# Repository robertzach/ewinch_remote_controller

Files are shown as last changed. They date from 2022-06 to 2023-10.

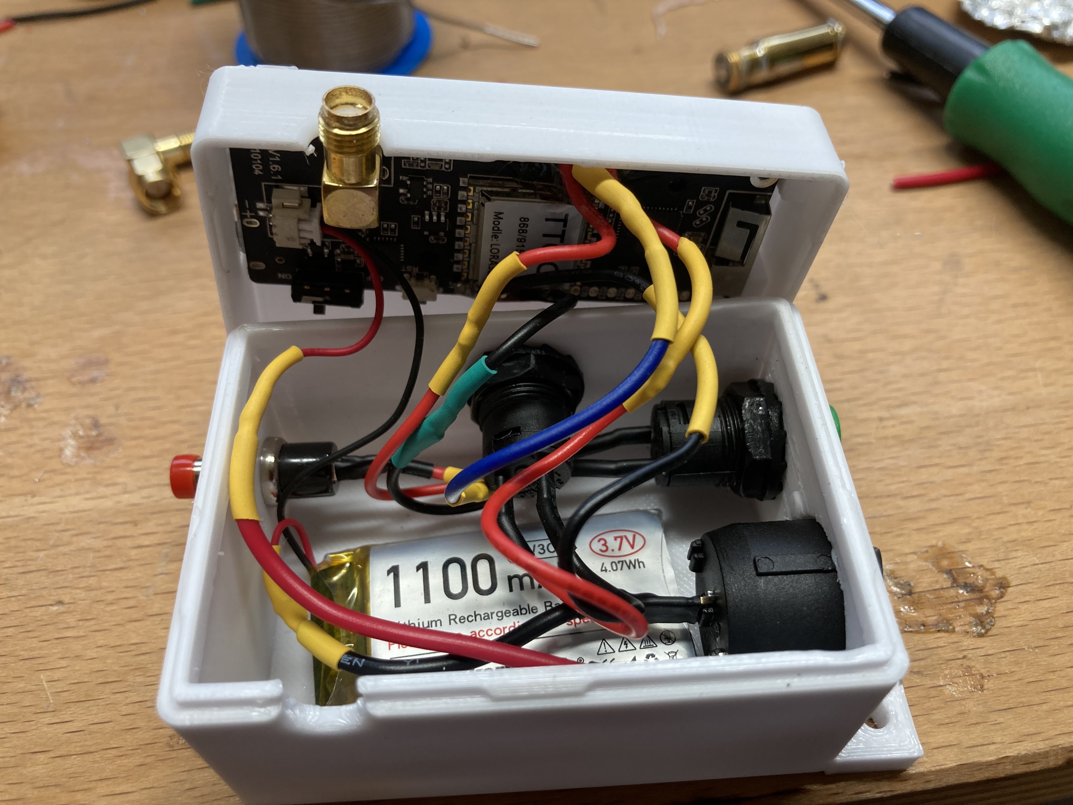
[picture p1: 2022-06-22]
doc/transmitter_cabels.jpg

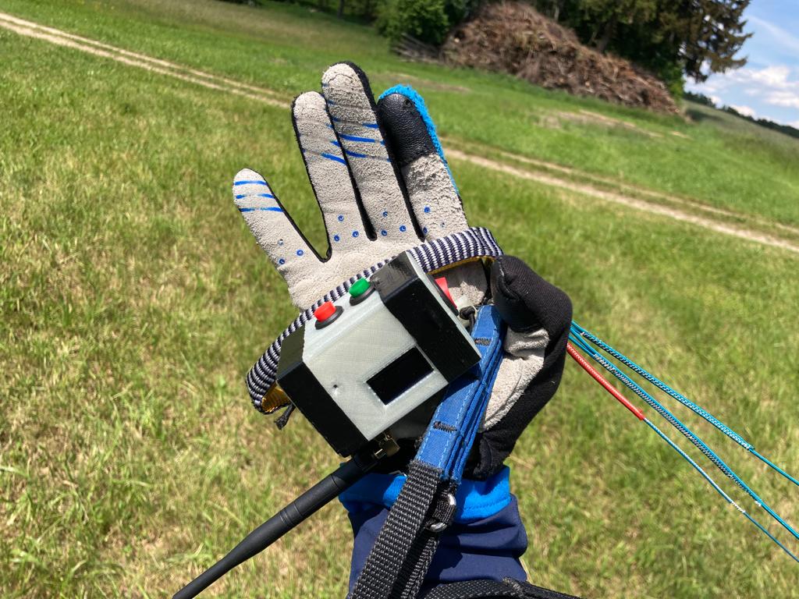
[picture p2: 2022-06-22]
doc/transmitter.jpg

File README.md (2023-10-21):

# ewinch_remote_controller
 transmitter and receiver code for remote controlling a paragliding winch
 Based on LILYGO® TTGO ESP32-Paxcounter LoRa32 V2.1 1.6 Version 915MHZ LoRa ESP-32 OLED
 (http://www.lilygo.cn/prod_view.aspx?TypeId=50060&Id=1271&FId=t3:50060:3)
 
 see 
 - https://www.youtube.com/watch?v=hUOhuwIBEUY
 - https://www.youtube.com/watch?v=hVimrIMGMSY&t=1s
 - https://www.youtube.com/watch?v=DOm1zkXft44
 - https://www.youtube.com/watch?v=bxIVrh16ZTE
 - https://www.youtube.com/watch?v=qTut_0KAwYU

 receiver uses PPM for driving the winch and (optinal) UART to read additional information (line length, battery %, dutycycle)
 VESC UART communication depends on https://github.com/SolidGeek/VescUart/

Pin Setup receiver:
PWM_PIN_OUT  13
VESC_RX  14    //connect to TX on Vesc
VESC_TX  2    //connect to RX on Vesc

transmitter buttons connected to GND:
BUTTON_UP  15 
BUTTON_DOWN  12

Line auto stop can be implemented within VESC with vesc_ppm_auto_stop.patch
Default VESC app config is vesc_app_config.xml

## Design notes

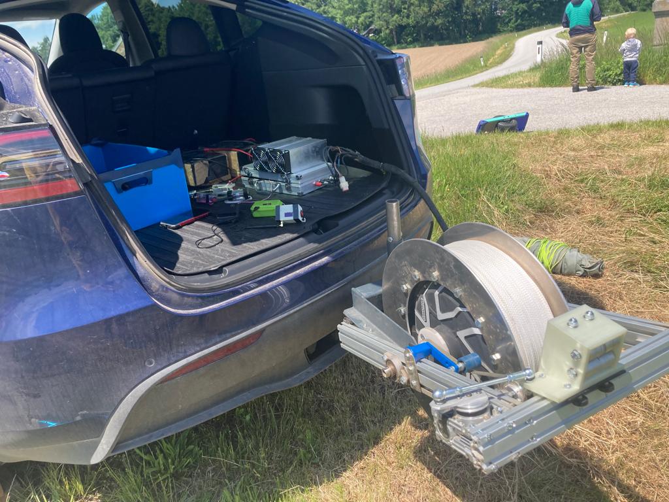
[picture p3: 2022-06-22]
doc/winch.jpg

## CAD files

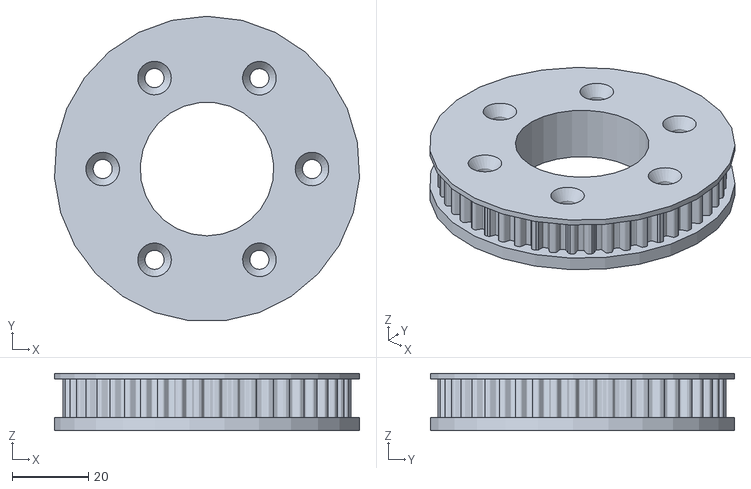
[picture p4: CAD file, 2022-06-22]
stl/belt_drive_B.stl
79.9 x 79.7 x 15.0

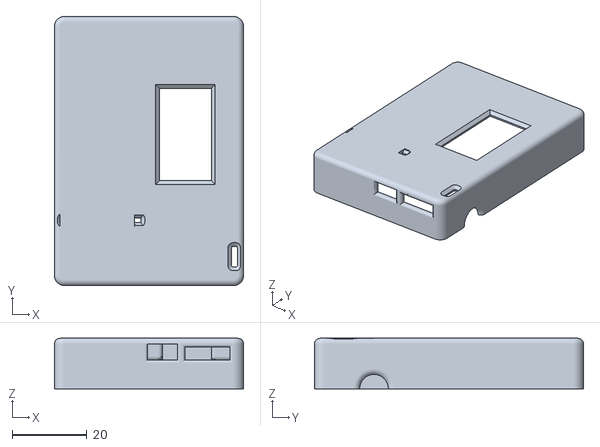
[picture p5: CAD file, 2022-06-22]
stl/transmitter_top.stl
50.6 x 71.9 x 13.5

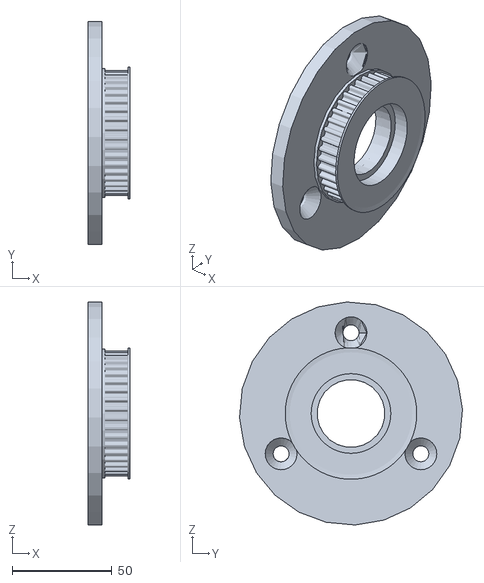
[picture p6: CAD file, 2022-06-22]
stl/belt_drive_A.stl
21.3 x 111.9 x 111.9

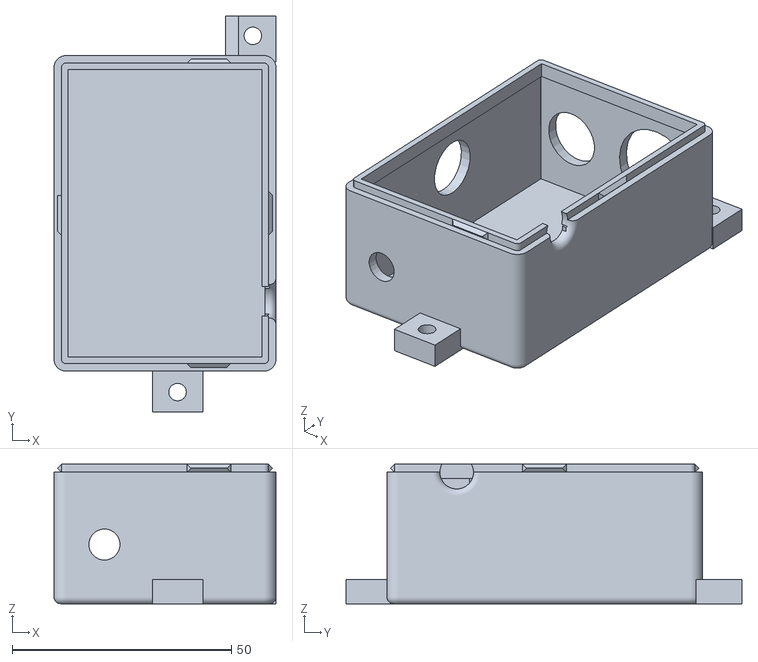
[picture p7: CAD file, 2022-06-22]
stl/transmitter_bottom.stl
50.6 x 90.2 x 31.8

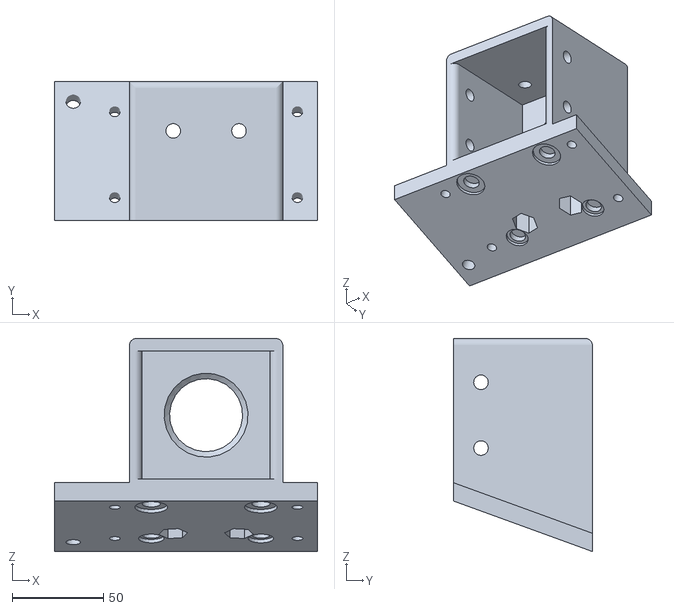
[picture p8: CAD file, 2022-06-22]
stl/cable_guide.stl
144.0 x 76.0 x 116.7

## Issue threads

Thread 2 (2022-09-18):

Battery Config / Voltage

looxis-renaud, 2022-09-18:
Not really an issue on the remote controller itself - but without the winch, there's no need for the remote :-)
why re-invent the wheel, so my plan is to build the winch exactly as you did, with the same components.

In one of your youtube comments you state that you use 2x 8S10P battery packs made from INR21700 cells.
Are you connecting the two packs in parallel (28,8 Volt) or in series (57,6 Volt) ?

looxis-renaud, 2022-09-18:
found the answer in the youtube comments :-)

> [@siffer siffer ](https://www.youtube.com/channel/UCgYK9i93dRLXB5Vw_T8CE_Q) see the pics in the link. twice 8s10p in series without BMS. 8s can be charged with common RC chargers...
>
> https://drive.google.com/drive/folders/1BV3k2qoKL2DN3fKvVQ9Kf_huecXmPUIT

Closed 2022-09-18.

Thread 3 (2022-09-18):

Motor

looxis-renaud, 2022-09-18:
In one of the youtube comments you mentioned that you are using the QS Motor 12kw,
available here: https://www.aliexpress.com/item/4001237537247.html

Do you use the **"72V"** or the **"96V"** version ?

robertzach, 2022-10-17:
Chinese supplier are a bit confusing with their order options.
The main thing is the "KV" value which describes the rpm / voltage relation.
rpm = KV * voltage

Therefore, it depends on what battery voltage you use.
With a 16s lion battery (what I use) you have around 16*3,7 --> 60V.
For this case I recommend the 72V option (72V @ 1047RPM --> KV = 14).

steve1428, 2023-04-05:
be careful, I Found some other people representing themselves as QS motor when they weren't.  Deal with them directly.

Closed 2022-10-17.

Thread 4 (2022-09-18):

automatic brake with 15m of cable left

looxis-renaud, 2022-09-18:
How does the controller know after release, that it is time to brake because the line has only 15m left?

Is that calculated based on number of rotations of the drum, or is there a (magnetic) sensor on the cable, that detects the last 15m ?

robertzach, 2022-10-17:
the controller counts the rotations... it is very accurate!

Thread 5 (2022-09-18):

Which firmware for VESC Controller?

looxis-renaud, 2022-09-18:
VESC is controlling the brushless DC motor - do you use the standard VESC Firmware
or a fork? Asking this question because in one of your youtube videos you mention "Skypuff" which seems to be a fork of VESC standard firmware. I found this: https://github.com/talkyoo/vesc_tool_skypuff

robertzach, 2022-10-17:
It uses standard Vesc. e.g. 5.3.
Autostop is only supported with some changes in the standard vesc code:
see vesc/vesc_ppm_auto_stop.patch

looxis-renaud, 2022-10-18:
Hello Robert, I assume I could just use /vesc/vesc_75_300_auto_stop.bin,
which is probably the newly compiled VESC firmware including your vesc/vesc_ppm_auto_stop.patch ?

I do have the VESC 75/300.

_______
yes, I do not have any coding skills, I am just able to read and possibly understand the most basic code...

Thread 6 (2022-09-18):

parts needed for controlling the brushless DC Motor?

looxis-renaud, 2022-09-18:
watching your videos, I assume one needs the following electronics to control a brushless dc motor:

* VESC Controller
* Receiver: 1x LILYGO® TTGO ESP32-Paxcounter connected with VESC
* Transceiver 2x LILYGO® TTGO ESP32-Paxcounter, 1x Master & 1x Slave

Is this correct, or is anything else needed?

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

robertzach, 2022-10-17:
basically yes.
If multiple transmitter are used I would describe it as "admin" and "user" transmitters...

Closed 2022-10-17.

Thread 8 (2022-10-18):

Cable Guide parts

looxis-renaud, 2022-10-18:
I'd be happy to get some help on your cable guide.

I started a parts list for others to possibly follow up, but some of the parts are still unclear: https://github.com/looxis-renaud/ewinch_remote_controller/blob/main/doc/parts-list.md

It looks like you're using a worm gear. Any words on the gear ratio and the other parts that you used?

looxis-renaud, 2023-02-22:
I am not quite there yet, but in the meantime I am favoring a "level winder / barrel cam mechanism" as seen here: https://www.youtube.com/shorts/LLIwVdaRViM

Closed 2023-03-02.

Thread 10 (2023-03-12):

Moving "AutoStop" function from VESC to Receiver

looxis-renaud, 2023-03-12:
Since the receiver has Tachometer Data through the UART connection and "knows" the line length,
why not move the "AutoSTOP" feature from the VESC to the Receiver?

The Receiver is already controlling the winch, why not also let it execute the AutoStop when the line has only ~15m left?

The advantage would be that we could use the latest VESC firmware, without having to constantly change it by adding the Autostop feature ( I can't get the modified firmware to run anyways, see #9 )

robertzach, 2023-03-12:
It is already implemented it in the receiver code too (see line 277 to 292).
But it is slow (UART) and not 100% reliable (and you want 100%!).

See https://github.com/robertzach/ewinch_remote_controller/blob/main/receiver/receiver.ino:
      // auto line stop
      // (smouth to avoid line issues on main winch with rewinding winch)
      // tachometer > 2 --> avoid autostop when no tachometer values are read from uart (--> 0)
      if (vescUART.data.tachometer > 2 && vescUART.data.tachometer < 40) {
          if (targetPullValue > defaultPull){
              targetPullValue = defaultPull;
          }
          if (vescUART.data.tachometer < 20) {
              targetPullValue = softBrake;
          }
          if (vescUART.data.tachometer < 10) {
              targetPullValue = hardBrake;
          }
          Serial.println("Autostop active, target pull value:");
          Serial.println(targetPullValue);
      }

Closed 2023-03-12.

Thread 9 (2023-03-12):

vesc_75_300_auto_stop.bin makes the motor spin without stopping

looxis-renaud, 2023-03-12:
Hello Robert,
I had no luck flashing this firmware onto the VESC 75/300.
once you start setting up the input with this firmware, the motor just starts spinning and isn't controllable with your remote.
It does work with the original firmware, though (just no autostop then...)

I assume this is because of this function:

```
        // my default pull
        // manualy regulate pull with a poti on ADC2
        // in manual pull mode autostop only on demand (to rewind the last meters cable...)
   #ifdef ADC_IND_EXT2
     if ( (((float)ADC_Value[ADC_IND_EXT2])/4095) * V_REG > 0.5) {
     my_default_pull = ((((float)ADC_Value[ADC_IND_EXT2])/4095) * V_REG - 0.5) * 30;	//0 - 100% after 0.5V
        // set default pull value
     mc_interface_set_current(my_default_pull * 0.35);	//0 - 35A
```

This sounds like as it would be an early version of your code, where you were using a potentiometer to test the motor?
ADC2 input is not used, it's the PPM input that's being used... which has no ability to control the motor with this firmware.

I am just speculating here... sorry to bother.

robertzach, 2023-03-12:
I have a poti on ADC2 to manually control the winch. E.g. To wind up the last meters of the line when finishing. Or to set a tension when used as a rewind winch...

If you do not install one, just connect ADC2 to GND.

looxis-renaud, 2023-03-27:
@robertzach , can you tell me what specifications your potentiometer has ? i.e. the resistance, like 0,1, 1, 10 or even 100 kOhm ?

Closed 2023-03-12.

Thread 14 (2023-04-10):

ESP32 version?

steve1428, 2023-04-10:
code is sticking on esp32 version

cannot find crt1-sim.o: No such file or directory

do we know what version this code used?

steve1428, 2023-04-11:
just had to add esp-32 in preferences board manager urls

Closed 2023-04-11.

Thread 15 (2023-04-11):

work for hall

steve1428, 2023-04-11:
do you think the code will work for a hall sensor motor?
it looks like it was written for AS5047 SPI encoder

Closed 2023-04-14.

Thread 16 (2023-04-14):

No display, nothing happening

steve1428, 2023-04-14:
We got the ttgo t3 v 1.6.1 esp32 lora.  We found all the libraries and got the code to compile.  Tried loading the binary files as well as the code directly from arduino

no display working.
Try the Tx up down buttons, no pwm signals on the Rx pinout
there is an issue with ssd1306 library maybe and commands to setup the display?
the adafruit example sketch for 128X32 I2C works no problem, we can blink led etc so controller is working.
was there also supposed to include adafruit_1360 and gfx libraries maybe?

steve1428, 2023-04-15:
OLED pins are 21 and 22 on the controller, change in lines 84 thru 88 in the transmitter code and appropriate in receiver code.
we have display now but it's blinking on and off all the time

Closed 2023-04-15.

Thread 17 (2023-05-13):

VESC: Motor is "pumping" under heavy load, is this normal?

looxis-renaud, 2023-05-13:
Sorry Robert to bother you again.
I am ready to make a test flight, but we're having an issue:
 we wanted to test the motor's drag force according to the defined force in the remote, before we are actually going to launch ourselves.

We attached a "Quad" (a motorcycle with 4 wheels) to the line and started pulling. To measure the drag force in kilogram (or daN) we were using heavily the brake of the quad.

As you can see in this video: https://youtu.be/rusCd4p7q5k
the Motor is pumping /oscillating heavily under load.

When driving backwards under load, the winch was nicely unwinding the line, no issues with oscillation.

Is this possibly because of the inertia of the quad and because of the resistance of the wheels on the bumby grass?

Have you not experienced something similar?
Could this possibly be solved with some settings in the VESC app?

Thank you in advance for any help.

robertzach, 2023-05-15:
Looks like your VESC motor configuration is not very stable.
You can compare the pid values with the following config: https://github.com/robertzach/ewinch_remote_controller/blob/main/vesc/vesc_motor_config_12kw_260_V4.xml
Furthermore it is import that your winch is mounted on a more solid point to avoid oscillation!!
You can call me at +43 664 2314337, I may can give you some hints on the VESC motor config.
PS: Please also let me know were you got your thread for the line guide from? It looks really nice!

looxis-renaud, 2023-05-16:
Hi Robert,
thanks again, as always, for your valuable feedback. will check the VESC settings again and also give you a call.

The "line guide" or "winding mechanism" was purchased from https://www.ebinger-gmbh.com/
It's the model 1.610.010 >>automatische Schlauchführung, Stahl lackiert, 1/2" -/ 5/8" Schlauch für Modell OSM 610<<.
It's intended purpose is for water hoses or compressed air hoses and was modified by a friend of mine to accommodate for the thin dyneema line and the width of the drum.

Closed 2023-05-16.

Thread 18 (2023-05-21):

pinmode set for button up / dn

steve1428, 2023-05-21:
hi can you tell me please if pin 15 / 12 are internal pullup?
I can't see in the code.

is it possible to change to internal pulldown so we can trigger it with an external 3.3V signal?

robertzach, 2023-05-23:
yes, both use a internal pull up. I am not sure if you can reprogram it. Google is your friend :-).
Fast solutions would be a external 1k resistor to GND or use a different pin...

Closed 2023-05-23.

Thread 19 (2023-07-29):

Skalierung der Leistung

Logo66, 2023-07-29:
Hallo Robert Microkontroler programmieren usw. ist Neuland für mich. Habe eigentlich fast alles hingekriegt aber das eine oder andere versteh ich noch nicht ganz. z.B
In der Anweisung für PPM-Einstellungen heißt es: „static int myMaxPull = 85; // 0 – 127 [kg], muss mit den VESC-ppm-Einstellungen skaliert werden.“ Wie wird dies eingestellt oder kalibriert?

https://photos.app.goo.gl/PnyRyFPGkBvydZn87

steve1428, 2023-07-29:
I think he means you just vary the pull amount in the code depending on
your particular motor's power
if you notice he's made two of them so he can use the other one in braking
mode to test and set things up, otherwise you have to go out in a field and
do test pulls.
I've got mine all working I just need to 3D print the hand held controller
case because I can't find anything appropriate off the shelf
https://youtu.be/9rqX89-msBY

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

Logo66, 2023-07-29:
https://a360.co/3Dy5PxJ

Ich habe mir diesen gedruckt.

steve1428, 2023-07-29:
Das ist wunderschön !

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

steve1428, 2023-07-29:
https://d-splicer.com/d-splicer-set-kit/

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

robertzach, 2023-07-29:
Depending on your motor (power, KV value, diameter, etc.) you need to scale the resulting kg pull on your line.
I think the best way is to adapt the "Motor Current Max" and "Motor Current Max Brake" value in the Vesc Motor Settings (General -> Current).
You could also adapt the "Pulselength Start" and "Pulselength End" in the Vesc App settings (PPM -> Mapping) to reach the same goal.
I used a suitcase scale to measure the real pull on the line.
With my QS260 hub motor I have around ~3,6A/kg pull.

Logo66, 2023-07-29:
Danke Robert das hat mir weiter geholfen.

Closed 2023-07-29.

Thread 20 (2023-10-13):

QS motor

lamaatje, 2023-10-13:
Hi Robert,

In understand you use a 12kW QS motor 13" by 4.5" is that correct?
Did you order a specific variant optimized for torque?

Kind regards,
Stefan

robertzach, 2023-10-16:
I used https://de.aliexpress.com/item/4001237537247.html?gatewayAdapt=glo2deu
with standard config.
I reach about 60 km/h with my 16s battery and a pull force about 70kg with about 240A.

steve1428, 2023-10-16:
I shorted my trampa vesc trying to setup on my electric unicycle, we tried
solder new mosfets but didn't work.
There is cheaper vesc from India now

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

lamaatje, 2023-10-16:
Hi Robert,

Thanks for the response. I am looking for an appropriate motor it is my
understanding that many of those hub motors used in scooter/motorbike
applications are optimized for speed.
So am looking for something with high Kt [Nm/A] and high rated current.
I have a second hand QS motor that just does that but it does not have a
type tag. I can pull 70kg with 100A with a radius of .25m
this means 700/4= 125Nm @ 100A -> Kt = 1,25 Nm/A.
I am not sure what you diameter is but lets also take .25m than your
motors Kt = 125/240 = 0,52 Nm/A.  Since motor dissipation is mainly due
to copper loss I2R, lower current is very desirable to avoid motor
heating. Of course with low R heating can also be avoided that is why it
is important to know the rated current. For your motor I understand that
this is 167A so that means it will heat up considerable.
Can you confirm this?

Kind regards,

Stefan

robertzach schreef op 2023-10-16 10:10:
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

steve1428, 2023-10-16:
yup, hub motors aren't really designed for high torque applications so they
get hot.
setup a fan and keep an eye on the temps.
If you look at other winch projects on youtube some guys are using other
motor types.

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

lamaatje, 2023-10-16:
Well there is not a fundamental reason why they could not be optimized for torque and since they have high pole pairs counts they can deliver quite a lot of power in the RPM range for a paraglider winch applications. Although the high rotational inertia is also a big disadvantage. The big advantage is direct drive. Do you have some pointers wrt other QS motor or hub motors in general?

steve1428, 2023-10-16:
yes they do make very high torque BLDC motors..... the leperkim veteran
patton electric unicycle (126V) I just bought has enough torque to spin the
wheel when you climb a hill, it's a beast.

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

robertzach, 2023-10-16:
**If you want to do step tows you need some speed to be safe when flying back!!!**
If you do no step tows you can go down with the speed to around 40km/h -> choose a hub motor with lower KV value (more torque optimized)
My first winch was calculated for max speed around 40 km/h (see https://www.youtube.com/watch?v=E3TgccQ8CuA).
It also depends on what battery you want to use.
Right now I am using 16s which is 66V on full charge. This keep my battery setup easy.
For my first winch I increased to 22s (90V) to get more speed.
To sum up, battery/controller/motor needs to be chosen in the right mix, depending on your speed (step tows?) and pull (weight?) requirements.

lamaatje, 2023-10-16:
Hi Robert,
I have to disagree. When step towing and flying away from the winch the motor just needs to brake. The torque is opposite to the rotation direction so you will be generating power. E.g. say you fly away from the winch with 15 m/s and the tow force is 40N (towards the winch ie the same direction as when doing a tow) you will be generating 600W. Assuming no losses for simplicity, if your battery is 60V you will be charging it with 10A.

Towing requirements are simple in zero wind conditions 10 m/s @ 1000N. So 10kW mechanical power.  So a 12 kW rated motor should be able to do the job. 12kW is the electrical rating assuming 10/12=83% efficiency at the rated mechanical power this is realistic. Depending on your spool radius you need a motor with the proper Torque, speed curve where the RPM at maximum power is at 10 m/s. For a radius of 0.2m that would be 477 RPM and 200Nm.

steve1428, 2023-10-16:
12KW is plenty of power regardless

I've got the QS motor 3/5 kw motor and I know people are able to get it to
work

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

robertzach, 2023-10-17:
I recommend you https://en.wikipedia.org/wiki/Motor_constants
Max speed is defined by KV = speed / Voltage.
The only way to increase speed above the limit based on KV and Voltage is to use field weakening.
But field weakening is still beta in VESC and in my tests it only increased the max. speed with my hub motors around 20%.
I would not recommend to used field weakening to increase max. speed for flying away on step tows.
If anything fails you can get in big trouble....

lamaatje, 2023-10-17:
I think you are missing the point here. All these things like field weakening to increase speed are applicable when the motor is **driving**. When you fly away from the winch the motor is not supposed to be driving it is supposed to be **breaking**.  If you look to it from another perspective: suppose that you completely shut down the motor control when you fly away from the winch will your speed be limited? I think the answer is no. Is it is also not desirable because you need some force to limit slack of the line and make sure the line stays on the spool. You can do this by letting the motor brake a bit this can be done at rpm's way higher than the rpm's in the range were the motor is driven. You have to basically control the current the motor is **generating** (NB not consuming) and the best way is to have the current back in the battery (regen braking). The speed range were you can do regen braking is much higher and mainly voltage limited. I have this working on my controller and it works just fine.

lamaatje, 2023-10-17:
> 12KW is plenty of power regardless I've got the QS motor 3/5 kw motor and I know people are able to get it to work
> […](#)
Sure, with a little bit of head wind, low pilot weight, low ascend rate. But that is not the point. If your motor is capable of a certain sustainable mechanical power you want to dimension it in such a way that it gives that output in a range that is optimal for towing that's why you do the math.

robertzach, 2023-10-17:
> when you fly away from the winch will your speed be limited? I think the answer is no

This is wrong. For brushless motor rpm and voltage are in direct correlation.
Therefore, when you increase the motor rpm (when flying away) above the limit (which is the voltage of the controller) the controller will burn. By using field weakening you can push this limit a bit, but any issue will immediately burn the controller.
When you burn the controller when flying away I wish you that the lines on the spool do not get messed up.
Yes, it is possible to a 5kW hub motor, but you will be very likely limited with speed supported...

steve1428, 2023-10-17:
doesn't the BMS deal with the regen current?  This is a problem with
electric unicycles going down hill after a full charge.
as long as the battery isn't 100% the regen will go to the battery no?

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

robertzach, 2023-10-17:
The hardware diagram is:
motor ---  controller --- battery (incl. BMS)
If the controller can't deal with the voltage of the motor you don't have to worry about the battery.
The controller will be dead in a few seconds anyway.

lamaatje, 2023-10-17:
*This is wrong.
No there is no force holding you back.

*For brushless motor rpm and voltage are in direct correlation.
That is correct that is why I state "The speed range were you can do regen braking is much higher and mainly voltage limited." so I agree that your controller has to be able to deal with the voltages but that is a **controller property**

*By using field weakening you can push this limit a bit, but any issue will immediately burn the controller. When you burn the *controller when flying away I wish you that the lines on the spool do not get messed up.
No field weakening has nothing to do with it. Yes if voltages are higher than the MOSFET Vds breakdown voltage that is a problem but it is controller related. I have a motor when driving it at zero load reaches 634 RPM the voltage is than around 70V that is a **motor property**. The torque is than long gone and my tow line speed is than around 55 kmh. So when driving the motor the RPM is limited because the back-EMF reaches input voltage of 70V. With field weakening you actively can reduce the back-EMF and gain a little speed or you can increase the voltage when driving the motor. My controller can handle 120V so when I fly back in windy conditions with 70 kmh the motor will generate around 90V and there is not issue whatsoever to do controlled EM braking.
So when choosing your motor's Kv the step tow fly back speed is not a real consideration just make sure you have a controller that can deal with the generated voltage.

robertzach, 2023-10-21:
I am interested in your controller which can handle 120V.
Which one is it?

steve1428, 2023-10-21:
are you asking me because I mentioned my 126V veteran patton EUC?

it's the controller the mfg put on it.

The 3SHUL makes a controller for that voltage, you can see their products
here

https://alienrides.com/collections/3shul-vesc-motor-controllers/products/3shul-vesc-motor-controller-c1400

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

lamaatje, 2023-10-21:
Hi Robert,

It is a sevcon gen4 96-120V. I included an overview pdf. The 72-80V
variants already support up to 116V DC maximum operating voltage so that
would be also a good choice in this example.
I also have a question to you wrt the QS motor you purchased was it with
rim? I understand it is also possible to order them without rim in that
case the minimum spool diameter can be a bit smaller which gives more
tuning bandwith to match the motor torque speed curve.

robertzach schreef op 2023-10-21 22:01:
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

steve1428, 2023-10-22:
I would warn people away from buying the Trampa VESC, it's designed to fit
in an electric skateboard, very compact and delicate, surface mount mosfet,
microscopic gate drivers and associated components positioned close by,
it's next to impossible to repair and easily damaged.

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

robertzach, 2023-10-22:
3SHUL VESC controller look really good!
Do you have experience with the CL350?
(https://alienrides.com/collections/3shul-vesc-motor-controllers/products/3shul-vesc-motor-controller-cl350)

steve1428, 2023-10-22:
no but check out Luke F youtube channel, he is using one for his winch,
i'll post the link to his video but I don't know if github allows.
if not look for:
"Playing music on the hang glider winches motor stator"

https://youtu.be/fslWr41YOQk?feature=shared

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

lamaatje, 2023-10-22:
I saw there is also a European dealer but the 350CL is only on presale. Very affordable compared a commercial controller. Does VESC have an API or protocol to write application?
-------- Original message --------From: robertzach ***@***.***> Date: 10/22/23  3:27 PM  (GMT+01:00) To: robertzach/ewinch_remote_controller ***@***.***> Cc: lamaatje ***@***.***>, Author ***@***.***> Subject: Re: [robertzach/ewinch_remote_controller] QS motor (Issue #20)
3SHUL VESC controller look really good!
Do you have experience with the CL350?
(https://alienrides.com/collections/3shul-vesc-motor-controllers/products/3shul-vesc-motor-controller-cl350)

—Reply to this email directly, view it on GitHub, or unsubscribe.You are receiving this because you authored the thread.Message ID: ***@***.***>

steve1428, 2023-10-22:
i dunno bout this expensive high voltage dc stuff, check out what this guy
is doing with the GY6 drivetrain

https://youtu.be/VPotT-ulV7g?feature=shared

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

Closed 2023-10-17.

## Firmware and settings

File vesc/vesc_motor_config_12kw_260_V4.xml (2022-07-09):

<?xml version="1.0" encoding="UTF-8"?>
<MCConfiguration>
    <ConfigVersion>2</ConfigVersion>
    <pwm_mode>1</pwm_mode>
    <comm_mode>0</comm_mode>
    <motor_type>2</motor_type>
    <sensor_mode>0</sensor_mode>
    <l_current_max>250</l_current_max>
    <l_current_min>-250</l_current_min>
    <l_in_current_max>290</l_in_current_max>
    <l_in_current_min>-290</l_in_current_min>
    <l_abs_current_max>290</l_abs_current_max>
    <l_min_erpm>-100000</l_min_erpm>
    <l_max_erpm>100000</l_max_erpm>
    <l_erpm_start>0.8</l_erpm_start>
    <l_max_erpm_fbrake>300</l_max_erpm_fbrake>
    <l_max_erpm_fbrake_cc>1500</l_max_erpm_fbrake_cc>
    <l_min_vin>12</l_min_vin>
    <l_max_vin>72</l_max_vin>
    <l_battery_cut_start>54.4</l_battery_cut_start>
    <l_battery_cut_end>49.6</l_battery_cut_end>
    <l_slow_abs_current>0</l_slow_abs_current>
    <l_temp_fet_start>85</l_temp_fet_start>
    <l_temp_fet_end>100</l_temp_fet_end>
    <l_temp_motor_start>75</l_temp_motor_start>
    <l_temp_motor_end>85</l_temp_motor_end>
    <l_temp_accel_dec>0.01</l_temp_accel_dec>
    <l_min_duty>0.005</l_min_duty>
    <l_max_duty>0.95</l_max_duty>
    <l_watt_max>1.5e+06</l_watt_max>
    <l_watt_min>-1.5e+06</l_watt_min>
    <l_current_max_scale>1</l_current_max_scale>
    <l_current_min_scale>1</l_current_min_scale>
    <l_duty_start>1</l_duty_start>
    <sl_min_erpm>150</sl_min_erpm>
    <sl_min_erpm_cycle_int_limit>1100</sl_min_erpm_cycle_int_limit>
    <sl_max_fullbreak_current_dir_change>10</sl_max_fullbreak_current_dir_change>
    <sl_cycle_int_limit>62</sl_cycle_int_limit>
    <sl_phase_advance_at_br>0.8</sl_phase_advance_at_br>
    <sl_cycle_int_rpm_br>80000</sl_cycle_int_rpm_br>
    <sl_bemf_coupling_k>600</sl_bemf_coupling_k>
    <hall_table__0>-1</hall_table__0>
    <hall_table__1>1</hall_table__1>
    <hall_table__2>3</hall_table__2>
    <hall_table__3>2</hall_table__3>
    <hall_table__4>5</hall_table__4>
    <hall_table__5>6</hall_table__5>
    <hall_table__6>4</hall_table__6>
    <hall_table__7>-1</hall_table__7>
    <hall_sl_erpm>2000</hall_sl_erpm>
    <foc_current_kp>0.0161</foc_current_kp>
    <foc_current_ki>5.82</foc_current_ki>
    <foc_f_zv>30000</foc_f_zv>
    <foc_dt_us>0.12</foc_dt_us>
    <foc_encoder_inverted>0</foc_encoder_inverted>
    <foc_encoder_offset>180</foc_encoder_offset>
    <foc_encoder_ratio>7</foc_encoder_ratio>
    <foc_encoder_sin_gain>1</foc_encoder_sin_gain>
    <foc_encoder_cos_gain>1</foc_encoder_cos_gain>
    <foc_encoder_sin_offset>1.65</foc_encoder_sin_offset>
    <foc_encoder_cos_offset>1.65</foc_encoder_cos_offset>
    <foc_encoder_sincos_filter_constant>0.5</foc_encoder_sincos_filter_constant>
    <foc_sensor_mode>2</foc_sensor_mode>
    <foc_pll_kp>2000</foc_pll_kp>
    <foc_pll_ki>30000</foc_pll_ki>
    <foc_motor_l>1.611e-05</foc_motor_l>
    <foc_motor_ld_lq_diff>4.59e-06</foc_motor_ld_lq_diff>
    <foc_motor_r>0.0058</foc_motor_r>
    <foc_motor_flux_linkage>0.025592</foc_motor_flux_linkage>
    <foc_observer_gain>1.53e+06</foc_observer_gain>
    <foc_observer_gain_slow>0.05</foc_observer_gain_slow>
    <foc_observer_offset>-1</foc_observer_offset>
    <foc_duty_dowmramp_kp>10</foc_duty_dowmramp_kp>
    <foc_duty_dowmramp_ki>200</foc_duty_dowmramp_ki>
    <foc_openloop_rpm>150</foc_openloop_rpm>
    <foc_openloop_rpm_low>0</foc_openloop_rpm_low>
    <foc_d_gain_scale_start>0.9</foc_d_gain_scale_start>
    <foc_d_gain_scale_max_mod>0.2</foc_d_gain_scale_max_mod>
    <foc_sl_openloop_hyst>0.1</foc_sl_openloop_hyst>
    <foc_sl_openloop_time_lock>0</foc_sl_openloop_time_lock>
    <foc_sl_openloop_time_ramp>0.1</foc_sl_openloop_time_ramp>
    <foc_sl_openloop_time>0.05</foc_sl_openloop_time>
    <foc_hall_table__0>255</foc_hall_table__0>
    <foc_hall_table__1>132</foc_hall_table__1>
    <foc_hall_table__2>198</foc_hall_table__2>
    <foc_hall_table__3>165</foc_hall_table__3>
    <foc_hall_table__4>66</foc_hall_table__4>
    <foc_hall_table__5>99</foc_hall_table__5>
    <foc_hall_table__6>33</foc_hall_table__6>
    <foc_hall_table__7>255</foc_hall_table__7>
    <foc_hall_interp_erpm>500</foc_hall_interp_erpm>
    <foc_sl_erpm>2000</foc_sl_erpm>
    <foc_sample_v0_v7>0</foc_sample_v0_v7>
    <foc_sample_high_current>0</foc_sample_high_current>
    <foc_sat_comp>0</foc_sat_comp>
    <foc_temp_comp>1</foc_temp_comp>
    <foc_temp_comp_base_temp>15.9</foc_temp_comp_base_temp>
    <foc_current_filter_const>0.1</foc_current_filter_const>
    <foc_cc_decoupling>0</foc_cc_decoupling>
    <foc_observer_type>0</foc_observer_type>
    <foc_hfi_voltage_start>20</foc_hfi_voltage_start>
    <foc_hfi_voltage_run>4</foc_hfi_voltage_run>
    <foc_hfi_voltage_max>10</foc_hfi_voltage_max>
    <foc_sl_erpm_hfi>2000</foc_sl_erpm_hfi>
    <foc_hfi_start_samples>15</foc_hfi_start_samples>
    <foc_hfi_obs_ovr_sec>0.001</foc_hfi_obs_ovr_sec>
    <foc_hfi_samples>1</foc_hfi_samples>
    <foc_offsets_cal_on_boot>1</foc_offsets_cal_on_boot>
    <foc_offsets_current__0>2044.2</foc_offsets_current__0>
    <foc_offsets_current__1>2044.41</foc_offsets_current__1>
    <foc_offsets_current__2>2044.68</foc_offsets_current__2>
    <foc_offsets_voltage__0>-0.0042</foc_offsets_voltage__0>
    <foc_offsets_voltage__1>0.0017</foc_offsets_voltage__1>
    <foc_offsets_voltage__2>0.0024</foc_offsets_voltage__2>
    <foc_offsets_voltage_undriven__0>0</foc_offsets_voltage_undriven__0>
    <foc_offsets_voltage_undriven__1>0</foc_offsets_voltage_undriven__1>
    <foc_offsets_voltage_undriven__2>0</foc_offsets_voltage_undriven__2>
    <foc_phase_filter_enable>1</foc_phase_filter_enable>
    <foc_phase_filter_max_erpm>4000</foc_phase_filter_max_erpm>
    <foc_mtpa_mode>0</foc_mtpa_mode>
    <foc_fw_current_max>100</foc_fw_current_max>
    <foc_fw_duty_start>0.9</foc_fw_duty_start>
    <foc_fw_q_current_factor>0.02</foc_fw_q_current_factor>
    <foc_fw_ramp_time>0.2</foc_fw_ramp_time>
    <gpd_buffer_notify_left>200</gpd_buffer_notify_left>
    <gpd_buffer_interpol>0</gpd_buffer_interpol>
    <gpd_current_filter_const>0.1</gpd_current_filter_const>
    <gpd_current_kp>0.03</gpd_current_kp>
    <gpd_current_ki>50</gpd_current_ki>
    <sp_pid_loop_rate>5</sp_pid_loop_rate>
    <s_pid_kp>0.004</s_pid_kp>
    <s_pid_ki>0.004</s_pid_ki>
    <s_pid_kd>0.0001</s_pid_kd>
    <s_pid_kd_filter>0.2</s_pid_kd_filter>
    <s_pid_min_erpm>900</s_pid_min_erpm>
    <s_pid_allow_braking>1</s_pid_allow_braking>
    <s_pid_ramp_erpms_s>25000</s_pid_ramp_erpms_s>
    <p_pid_kp>0.025</p_pid_kp>
    <p_pid_ki>0</p_pid_ki>
    <p_pid_kd>0</p_pid_kd>
    <p_pid_offset>0</p_pid_offset>
    <p_pid_kd_proc>0.00035</p_pid_kd_proc>
    <p_pid_kd_filter>0.2</p_pid_kd_filter>
    <p_pid_ang_div>1</p_pid_ang_div>
    <p_pid_gain_dec_angle>0</p_pid_gain_dec_angle>
    <cc_startup_boost_duty>0.01</cc_startup_boost_duty>
    <cc_min_current>0.05</cc_min_current>
    <cc_gain>0.0046</cc_gain>
    <cc_ramp_step_max>0.04</cc_ramp_step_max>
    <m_fault_stop_time_ms>0</m_fault_stop_time_ms>
    <m_duty_ramp_step>0.02</m_duty_ramp_step>
    <m_current_backoff_gain>0.5</m_current_backoff_gain>
    <m_encoder_counts>8192</m_encoder_counts>
    <m_sensor_port_mode>0</m_sensor_port_mode>
    <m_invert_direction>1</m_invert_direction>
    <m_drv8301_oc_mode>0</m_drv8301_oc_mode>
    <m_drv8301_oc_adj>16</m_drv8301_oc_adj>
    <m_bldc_f_sw_min>3000</m_bldc_f_sw_min>
    <m_bldc_f_sw_max>35000</m_bldc_f_sw_max>
    <m_dc_f_sw>25000</m_dc_f_sw>
    <m_ntc_motor_beta>3380</m_ntc_motor_beta>
    <m_out_aux_mode>11</m_out_aux_mode>
    <m_motor_temp_sens_type>2</m_motor_temp_sens_type>
    <m_ptc_motor_coeff>0.61</m_ptc_motor_coeff>
    <m_hall_extra_samples>1</m_hall_extra_samples>
    <si_motor_poles>32</si_motor_poles>
    <si_gear_ratio>1</si_gear_ratio>
    <si_wheel_diameter>0.38</si_wheel_diameter>
    <si_battery_type>0</si_battery_type>
    <si_battery_cells>16</si_battery_cells>
    <si_battery_ah>300</si_battery_ah>
    <si_motor_nl_current>1</si_motor_nl_current>
    <motor_brand>Unnamed</motor_brand>
    <motor_model>Not Specified</motor_model>
    <motor_weight>0</motor_weight>
    <motor_sensor_type>0</motor_sensor_type>
    <motor_description>&lt;!DOCTYPE HTML PUBLIC &quot;-//W3C//DTD HTML 4.0//EN&quot; &quot;http://www.w3.org/TR/REC-html40/strict.dtd&quot;&gt;
&lt;html&gt;&lt;head&gt;&lt;meta name=&quot;qrichtext&quot; content=&quot;1&quot; /&gt;&lt;style type=&quot;text/css&quot;&gt;
p, li { white-space: pre-wrap; }
&lt;/style&gt;&lt;/head&gt;&lt;body style=&quot; font-family:'Roboto'; font-size:12pt; font-weight:400; font-style:normal;&quot;&gt;
&lt;p style=&quot; margin-top:0px; margin-bottom:0px; margin-left:0px; margin-right:0px; -qt-block-indent:0; text-indent:0px;&quot;&gt;A motor description can be edited here.&lt;/p&gt;&lt;/body&gt;&lt;/html&gt;</motor_description>
    <motor_quality_bearings>0</motor_quality_bearings>
    <motor_quality_magnets>0</motor_quality_magnets>
    <motor_quality_construction>0</motor_quality_construction>
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

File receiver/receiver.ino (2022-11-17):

/*
 * receiver
 * receives target pull value from lora link
 * sends acknowlegement on lora with current parameters
 * writes target pull with PWM signal to vesc
 * reads current parameters (tachometer, battery %, motor temp) with UART from vesc, based on (https://github.com/SolidGeek/VescUart/)
 * 
 */

//vesc battery number of cells
static int numberOfCells = 16;
static int myMaxPull = 75;  // 0 - 127 [kg], must be scaled with VESC ppm settings

#include "LiPoCheck.h"    //to calculate battery % based on cell Voltage

#include <Pangodream_18650_CL.h>
#include <SPI.h>
#include <LoRa.h>
#include <Wire.h>  
#include "SSD1306.h"
#define SCK     5    // GPIO5  -- SX1278's SCK
#define MISO    19   // GPIO19 -- SX1278's MISnO
#define MOSI    27   // GPIO27 -- SX1278's MOSI
#define SS      18   // GPIO18 -- SX1278's CS
#define RST     14   // GPIO14 -- SX1278's RESET
#define DI0     26   // GPIO26 -- SX1278's IRQ(Interrupt Request)
#define BAND  868E6

SSD1306 display(0x3c, 21, 22);
int rssi = 0;
float snr = 0;
String packSize = "--";
String packet ;

#include <rom/rtc.h>
#include "Arduino.h"
#include <Button2.h>

// battery measurement
//#define CONV_FACTOR 1.7
//#define READS 20
Pangodream_18650_CL BL(35); // pin 34 old / 35 new v2.1 hw


//Using VescUart librarie to read from Vesc (https://github.com/SolidGeek/VescUart/)
#include <VescUart.h>
#define VESC_RX  14    //connect to TX on Vesc
#define VESC_TX  2    //connect to RX on Vesc
VescUart vescUART;

// PWM signal to vesc
#define PWM_PIN_OUT  13 //Define Digital PIN
#define PWM_TIME_0      950.0    //PWM time in ms for 0% , PWM below will be ignored!! need XXX.0!!!
#define PWM_TIME_100    2000.0   //PWM time in ms for 100%, PWM above will be ignored!!

static int loopStep = 0;
static uint8_t activeTxId = 0;

#include "common.h"
struct LoraTxMessage loraTxMessage;
struct LoraRxMessage loraRxMessage;

int smoothStep = 0;    // used to smooth pull changes
int hardBrake = -20;  //in kg
int softBrake = -8;  //in kg
int defaultPull = 8;  //in kg
int prePullScale = 20;      //in % of myMaxPull
int takeOffPullScale = 50;  //in % of myMaxPull
int fullPullScale = 80;     //in % of myMaxPull
int strongPullScale = 100;  //in % of myMaxPull

int currentId = 0;
int currentState = -1;
// pull value send to VESC --> default soft brake
// defined as int to allow smooth changes without overrun
int currentPull = softBrake;     // active range -127 to 127
int8_t targetPullValue = 0;    // received from lora transmitter or rewinding winch mode


uint8_t vescBattery = 0;
uint8_t vescTempMotor = 0;
unsigned long lastTxLoraMessageMillis = 0;
unsigned long previousTxLoraMessageMillis = 0;
unsigned long lastRxLoraMessageMillis = 0;
unsigned long previousRxLoraMessageMillis = 0;
uint32_t  pwmReadTimeValue = 0;
uint32_t  pwmWriteTimeValue = 0;
unsigned long lastWritePWMMillis = 0;
unsigned int loraErrorCount = 0;
unsigned long loraErrorMillis = 0;


void pulseOut(int pin, int us)
{
   digitalWrite(pin, HIGH);
   us = max(us - 20, 1);  //biase caused by digital write/read
   delayMicroseconds(us);
   digitalWrite(pin, LOW);
}

void setup() {
  Serial.begin(115200);

  //Setup UART port for Vesc communication
  Serial1.begin(115200, SERIAL_8N1, VESC_RX, VESC_TX);
  vescUART.setSerialPort(&Serial1);
  //vescUART.setDebugPort(&Serial);
  
  //OLED display
  pinMode(16,OUTPUT);
  pinMode(2,OUTPUT);
  digitalWrite(16, LOW);    // set GPIO16 low to reset OLED
  delay(50); 
  digitalWrite(16, HIGH); // while OLED is running, must set GPIO16 in high

  //lora init
  SPI.begin(SCK,MISO,MOSI,SS);
  LoRa.setPins(SS,RST,DI0);
  if (!LoRa.begin(868E6)) {   //EU: 868E6 US: 915E6
    Serial.println("Starting LoRa failed!");
    while (1);
  }
  LoRa.setTxPower(20, PA_OUTPUT_PA_BOOST_PIN);
  //LoRa.setSpreadingFactor(10);   // default is 7, 6 - 12
  LoRa.enableCrc();
  //LoRa.setSignalBandwidth(500E3);   //signalBandwidth - signal bandwidth in Hz, defaults to 125E3. Supported values are 7.8E3, 10.4E3, 15.6E3, 20.8E3, 31.25E3, 41.7E3, 62.5E3, 125E3, 250E3, and 500E3.

  // display init
  display.init();
  //display.flipScreenVertically();  

  //PWM Pins
  //pinMode(PWM_PIN_IN, INPUT);
  pinMode(PWM_PIN_OUT, OUTPUT);
  
  display.clear();
  display.setTextAlignment(TEXT_ALIGN_LEFT);
  display.setFont(ArialMT_Plain_10);
  Serial.printf("Starting Receiver \n");
  display.drawString(0, 0, "Starting Receiver");
}


void loop() {

 loopStep++;
 // TODO activate rewinding winch mode here
 if (true) {
    // screen
    if (loopStep % 10 == 0) {
      display.clear();
      display.setTextAlignment(TEXT_ALIGN_LEFT);
      display.setFont(ArialMT_Plain_10);  //10, 16, 24
      display.drawString(0, 0, currentId + String("-RX: (") + BL.getBatteryChargeLevel() + "%, " + rssi + "dBm, " + snr + ")");
      display.setFont(ArialMT_Plain_24);  //10, 16, 24
      if (currentState > 0){
          display.drawString(0, 11, String("P ") + currentState + ": (" + currentPull + "kg)");  
      } else {
          display.drawString(0, 11, String("B ") + currentState + ": (" + currentPull + "kg)");    
      }
      display.setFont(ArialMT_Plain_10);  //10, 16, 24
      //display.drawString(0, 36, String("Error / Uptime{min}: ") + loraErrorCount + " / " + millis()/60000);
      display.drawString(0, 36, String("B: ") + vescBattery + "%, M: " + vescTempMotor + "C");
      display.drawString(0, 48, String("Last TX / RX: ") + lastTxLoraMessageMillis/100 + " / " + lastRxLoraMessageMillis/100);
      display.display();
    }
    
    // LoRa data available?
    // packet from transmitter
    if (LoRa.parsePacket() == sizeof(loraTxMessage) ) {
          LoRa.readBytes((uint8_t *)&loraTxMessage, sizeof(loraTxMessage));
          // allow only one ID to control the winch at a given time
          // after 5 seconds without a message, a new id is allowed
          if (millis() > lastTxLoraMessageMillis + 5000){
            activeTxId = loraTxMessage.id;
          }
          // The admin id 0 can allways take over
          if (loraTxMessage.id == 0){
            activeTxId = loraTxMessage.id;
          }
          if (loraTxMessage.id == activeTxId && loraTxMessage.pullValue == loraTxMessage.pullValueBackup) {
              targetPullValue = loraTxMessage.pullValue;
              currentId = loraTxMessage.id;
              currentState = loraTxMessage.currentState;
              previousTxLoraMessageMillis = lastTxLoraMessageMillis;  // remember time of previous paket
              lastTxLoraMessageMillis = millis();
              rssi = LoRa.packetRssi();
              snr = LoRa.packetSnr();
              Serial.printf("Value received: %d, RSSI: %d: , SNR: %d \n", loraTxMessage.pullValue, rssi, snr);
              
              // send ackn after receiving a value
              delay(10);
              loraRxMessage.pullValue = currentPull;
              loraRxMessage.tachometer = abs(vescUART.data.tachometer)/1000;     // %100 --> in m, %10 --> to use only one byte for up to 2550m line lenght
              loraRxMessage.dutyCycleNow = abs(vescUART.data.dutyCycleNow * 100);     //in %
              // alternate vescBatteryPercentage and vescTempMotor value on lora link to reduce packet size
              if (loraRxMessage.vescBatteryOrTempMotor == 0){
                loraRxMessage.vescBatteryOrTempMotor = 1;
                loraRxMessage.vescBatteryOrTempMotorValue = vescBattery;
              } else {
                loraRxMessage.vescBatteryOrTempMotor = 0;
                loraRxMessage.vescBatteryOrTempMotorValue = vescTempMotor;
              }
              if (LoRa.beginPacket()) {
                  LoRa.write((uint8_t*)&loraRxMessage, sizeof(loraRxMessage));
                  LoRa.endPacket();
                  Serial.printf("sending Ackn currentPull %d: \n", currentPull);
                  lastRxLoraMessageMillis = millis();  
              } else {
                  Serial.println("Lora send busy");
              }
              
          } else {
            Serial.println("Wrong transmitter id or backup Value:");
            Serial.println(loraTxMessage.id);
            Serial.println(loraTxMessage.pullValue);
            Serial.println(loraTxMessage.pullValueBackup);
          }
     }
  
      // if no lora message for more then 1,5s --> show error on screen + acustic
      if (millis() > lastTxLoraMessageMillis + 1500 ) {
            //TODO acustic information
            //TODO  red disply
            display.clear();
            display.display();
            // log connection error
           if (millis() > loraErrorMillis + 5000) {
                loraErrorMillis = millis();
                loraErrorCount = loraErrorCount + 1;
           }
      }
      // Failsafe only when pull was active
      if (currentState >= 1) {
            // no packet for 1,5s --> failsave
            if (millis() > lastTxLoraMessageMillis + 1500 ) {
                 // A) keep default pull if connection issue during pull for up to 10 seconds
                 if (millis() < lastTxLoraMessageMillis + 20000) {
                    targetPullValue = defaultPull;   // default pull
                    currentState = 1;
                 } else {
                 // B) go to soft brake afterwards
                    targetPullValue = softBrake;     // soft brake
                    currentState = -1;
                 }
            }
      }
      

 } else {
      // rewinding winch mode
      // screen
      if (loopStep % 10 == 0) {
        display.clear();
        display.setTextAlignment(TEXT_ALIGN_LEFT);
        display.setFont(ArialMT_Plain_10);  //10, 16, 24
        display.drawString(0, 0, "rewinding winch mode");
        display.setFont(ArialMT_Plain_24);  //10, 16, 24
        display.drawString(0, 14, String(targetPullValue) + "/" + currentPull + "kg");
        display.display();
      }

      // small pull value on pull out
      // higher pull value on pull in
      if (vescUART.data.dutyCycleNow > 0.02){
        targetPullValue = 10;
      } else if (vescUART.data.dutyCycleNow < -0.02){
        targetPullValue = 17;
      } else {
        targetPullValue = -5; // no line movement --> soft brake
      }
      // ??? TODO higher pull value on fast pull out to avoid drum overshoot on line disconection ???
      
 }  // end rewind winch mode


      // auto line stop
      // (smouth to avoid line issues on main winch with rewinding winch)
      // tachometer > 2 --> avoid autostop when no tachometer values are read from uart (--> 0)
      if (vescUART.data.tachometer > 2 && vescUART.data.tachometer < 40) {
          if (targetPullValue > defaultPull){
              targetPullValue = defaultPull;
          }
          if (vescUART.data.tachometer < 20) {
              targetPullValue = softBrake;
          }
          if (vescUART.data.tachometer < 10) {
              targetPullValue = hardBrake;
          }
          Serial.println("Autostop active, target pull value:");
          Serial.println(targetPullValue);
      }
 
      // smooth changes
      // if brake --> immediately active
      if (targetPullValue < 0 ){
          currentPull = targetPullValue;
      } else {   
          // change rate e.g. max. 50 kg / second
          //reduce pull
          if (currentPull > targetPullValue) {
              smoothStep = 90 * (millis() - lastWritePWMMillis) / 1000;
              if ((currentPull - smoothStep) > targetPullValue)   //avoid overshooting
                  currentPull = currentPull - smoothStep;
              else
                  currentPull = targetPullValue;
          //increase pull
          } else if (currentPull < targetPullValue) {
              smoothStep = 65 * (millis() - lastWritePWMMillis) / 1000;
              if ((currentPull + smoothStep) < targetPullValue)   //avoid overshooting
                  currentPull = currentPull + smoothStep;
              else
                  currentPull = targetPullValue;
          }
          //Serial.println(currentPull);
          //avoid overrun
          if (currentPull < -127)
            currentPull = -127;
          if (currentPull > 127)
            currentPull = 127;
      }
      
      delay(10);
      //calculate PWM time for VESC
      // write PWM signal to VESC
      pwmWriteTimeValue = (currentPull + 127) * (PWM_TIME_100 - PWM_TIME_0) / 254 + PWM_TIME_0;     
      pulseOut(PWM_PIN_OUT, pwmWriteTimeValue);
      lastWritePWMMillis = millis();
      delay(10);    //RC PWM usually has a signal every 20ms (50 Hz)

      
      //read actual Vesc values from uart
      if (loopStep % 20 == 0) {
        if (vescUART.getVescValues()) {
            vescBattery = CapCheckPerc(vescUART.data.inpVoltage, numberOfCells);    // vesc battery in %
            vescTempMotor = vescUART.data.tempMotor;                                // motor temp in C            
            //SerialPrint(measuredVescVal, &DEBUGSERIAL);
            /*
            Serial.println(vescUART.data.tachometer);
            Serial.println(vescUART.data.inpVoltage);
            Serial.println(vescUART.data.dutyCycleNow);            
            Serial.println(vescUART.data.tempMotor);
            Serial.println(vescUART.data.tempMosfet);
            vescUART.printVescValues();
            */
          }
        else
          {
            //TODO send notification to lora
            //measuredVescVal.tachometer = 0;
            Serial.println("Failed to get data from VESC!");
          }
      }
}

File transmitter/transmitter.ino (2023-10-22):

/*
 * 
 * transmitter
 * sends current state (pull value)
 * receives acknowlegement with current parameters
 * 
 */
// communication is locked to a specific transmitter for 5 seconds after his last message
// admin ID 0 can allays take over communication
static int myID = 1;    // set to your desired transmitter id!!! [unique number from 1 - 15]
static int myMaxPull = 75;  // 0 - 127 [kg], must be scaled with VESC ppm settings

#include <Pangodream_18650_CL.h>
#include <SPI.h>
#include <LoRa.h>
#include <Wire.h>  
#include "SSD1306.h"
#define SCK     5    // GPIO5  -- SX1278's SCK
#define MISO    19   // GPIO19 -- SX1278's MISnO
#define MOSI    27   // GPIO27 -- SX1278's MOSI
#define SS      18   // GPIO18 -- SX1278's CS
#define RST     14   // GPIO14 -- SX1278's RESET
#define DI0     26   // GPIO26 -- SX1278's IRQ(Interrupt Request)
#define BAND  868E6

SSD1306 display(0x3c, 21, 22);
int rssi = 0;
float snr = 0;
String packSize = "--";
String packet ;


#include <rom/rtc.h>

#include "Arduino.h"
#include <Button2.h>

// battery measurement
//#define CONV_FACTOR 1.7
//#define READS 20
Pangodream_18650_CL BL(35); // pin 34 old / 35 new v2.1 hw

// Buttons for state machine control
#define BUTTON_UP  15 // up
#define BUTTON_DOWN  12 // down, 4 old / 12 new v2.1 hw

Button2 btnUp = Button2(BUTTON_UP);
Button2 btnDown = Button2(BUTTON_DOWN);

static int loopStep = 0;
bool toogleSlow = true;
int8_t targetPull = 0;   // pull value range from -127 to 127
int currentPull = 0;          // current active pull on vesc
bool stateChanged = false;
int currentState = -1;   // -2 = hard brake, -1 = soft brake, 0 = no pull/no brake, 1 = default pull (~3kg), 2 = pre pull, 3 = take off pull, 4 = full pull, 5 = extra strong pull
int hardBrake = -20;  //in kg
int softBrake = -7;  //in kg
int defaultPull = 7;  //in kg
int prePullScale = 20;      //in %
int takeOffPullScale = 55;  //in %
int fullPullScale = 80;     //in %
int strongPullScale = 100;  //in %
unsigned long lastStateSwitchMillis = 0;

uint8_t vescBattery = 0;
uint8_t vescTempMotor = 0;

#include "common.h"
struct LoraTxMessage loraTxMessage;
struct LoraRxMessage loraRxMessage;

unsigned long lastTxLoraMessageMillis = 0;    //last message send
unsigned long lastRxLoraMessageMillis = 0;    //last message received
unsigned long previousRxLoraMessageMillis = 0;

unsigned int loraErrorCount = 0;
unsigned long loraErrorMillis = 0;


void setup() {
  Serial.begin(115200);
  
  //OLED display
  pinMode(16,OUTPUT);
  pinMode(2,OUTPUT);
  digitalWrite(16, LOW);    // set GPIO16 low to reset OLED
  delay(50); 
  digitalWrite(16, HIGH); // while OLED is running, must set GPIO16 in high

  //lora init
  SPI.begin(SCK,MISO,MOSI,SS);
  LoRa.setPins(SS,RST,DI0);
  if (!LoRa.begin(868E6)) {   //EU: 868E6 US: 915E6
    Serial.println("Starting LoRa failed!");
    while (1);
  }
  LoRa.setTxPower(20, PA_OUTPUT_PA_BOOST_PIN);
  //LoRa.setSpreadingFactor(10);   // default is 7, 6 - 12
  LoRa.enableCrc();
  //LoRa.setSignalBandwidth(500E3);   //signalBandwidth - signal bandwidth in Hz, defaults to 125E3. Supported values are 7.8E3, 10.4E3, 15.6E3, 20.8E3, 31.25E3, 41.7E3, 62.5E3, 125E3, 250E3, and 500E3.

  // display init
  display.init();
  //display.flipScreenVertically();  

  //Serial.println(" Longpress Time: " + String(btnUp.getLongClickTime()) + "ms");
  //Serial.println(" DoubleClick Time: " + String(btnUp.getDoubleClickTime()) + "ms");
  btnUp.setClickHandler(btnPressed);  //not called on long click
  btnUp.setLongClickTime(500);
  btnUp.setLongClickDetectedHandler(btnUpLongClickDetected);
  btnDown.setPressedHandler(btnPressed);
  btnDown.setLongClickTime(500);
  btnDown.setLongClickDetectedHandler(btnDownLongClickDetected);
  btnDown.setDoubleClickTime(400);
  btnDown.setDoubleClickHandler(btnDownDoubleClick);
    
  display.clear();
  display.setTextAlignment(TEXT_ALIGN_LEFT);
  display.setFont(ArialMT_Plain_10);
  Serial.printf("Starting Transmitter \n");
  display.drawString(0, 0, "Starting Transmitter");

  // admin --> scan for existing transmitter for a few seconds --> start up with his current pull state
  if (myID == 0 ) {
      display.clear();
      display.setTextAlignment(TEXT_ALIGN_LEFT);
      display.setFont(ArialMT_Plain_16);
      display.drawString(0, 0, "Searching 4s for");
      display.drawString(0, 14, "existing transmitter...");
      display.display();
      lastTxLoraMessageMillis = millis();
      while (millis() < lastTxLoraMessageMillis + 4000) {
          // packet from transmitter
          if (LoRa.parsePacket() >= sizeof(loraTxMessage) ) {
            LoRa.readBytes((uint8_t *)&loraTxMessage, sizeof(loraTxMessage));
            if (loraTxMessage.pullValue == loraTxMessage.pullValueBackup) {
                //found --> read state and exit
                currentState = loraTxMessage.currentState;
                targetPull = loraTxMessage.pullValue;
                Serial.printf("Found existing transmitter, starting up with state: %d: %d \n", currentState, targetPull);
                //exit search loop
                lastTxLoraMessageMillis = millis() - 4000;
            }
          } 
          delay(10);
       }
   }

   // reset to my transmitter id
   loraTxMessage.id = myID;
  
}
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

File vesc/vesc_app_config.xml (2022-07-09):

<?xml version="1.0" encoding="UTF-8"?>
<APPConfiguration>
    <ConfigVersion>2</ConfigVersion>
    <controller_id>111</controller_id>
    <timeout_msec>1000</timeout_msec>
    <timeout_brake_current>10</timeout_brake_current>
    <send_can_status>0</send_can_status>
    <send_can_status_rate_hz>50</send_can_status_rate_hz>
    <can_baud_rate>2</can_baud_rate>
    <pairing_done>0</pairing_done>
    <permanent_uart_enabled>1</permanent_uart_enabled>
    <shutdown_mode>9</shutdown_mode>
    <can_mode>0</can_mode>
    <uavcan_esc_index>0</uavcan_esc_index>
    <uavcan_raw_mode>0</uavcan_raw_mode>
    <uavcan_raw_rpm_max>50000</uavcan_raw_rpm_max>
    <servo_out_enable>0</servo_out_enable>
    <kill_sw_mode>0</kill_sw_mode>
    <app_to_use>4</app_to_use>
    <app_ppm_conf.ctrl_type>3</app_ppm_conf.ctrl_type>
    <app_ppm_conf.pid_max_erpm>15000</app_ppm_conf.pid_max_erpm>
    <app_ppm_conf.hyst>0.03</app_ppm_conf.hyst>
    <app_ppm_conf.pulse_start>1.1</app_ppm_conf.pulse_start>
    <app_ppm_conf.pulse_end>1.768</app_ppm_conf.pulse_end>
    <app_ppm_conf.pulse_center>1.459</app_ppm_conf.pulse_center>
    <app_ppm_conf.median_filter>1</app_ppm_conf.median_filter>
    <app_ppm_conf.safe_start>0</app_ppm_conf.safe_start>
    <app_ppm_conf.throttle_exp>0</app_ppm_conf.throttle_exp>
    <app_ppm_conf.throttle_exp_brake>0</app_ppm_conf.throttle_exp_brake>
    <app_ppm_conf.throttle_exp_mode>1</app_ppm_conf.throttle_exp_mode>
    <app_ppm_conf.ramp_time_pos>1</app_ppm_conf.ramp_time_pos>
    <app_ppm_conf.ramp_time_neg>0.5</app_ppm_conf.ramp_time_neg>
    <app_ppm_conf.multi_esc>0</app_ppm_conf.multi_esc>
    <app_ppm_conf.tc>0</app_ppm_conf.tc>
    <app_ppm_conf.tc_max_diff>3000</app_ppm_conf.tc_max_diff>
    <app_ppm_conf.max_erpm_for_dir>4000</app_ppm_conf.max_erpm_for_dir>
    <app_ppm_conf.smart_rev_max_duty>0.07</app_ppm_conf.smart_rev_max_duty>
    <app_ppm_conf.smart_rev_ramp_time>3</app_ppm_conf.smart_rev_ramp_time>
    <app_adc_conf.ctrl_type>0</app_adc_conf.ctrl_type>
    <app_adc_conf.hyst>0.15</app_adc_conf.hyst>
    <app_adc_conf.voltage_start>0.9</app_adc_conf.voltage_start>
    <app_adc_conf.voltage_end>3</app_adc_conf.voltage_end>
    <app_adc_conf.voltage_center>2</app_adc_conf.voltage_center>
    <app_adc_conf.voltage2_start>0.9</app_adc_conf.voltage2_start>
    <app_adc_conf.voltage2_end>3</app_adc_conf.voltage2_end>
    <app_adc_conf.use_filter>1</app_adc_conf.use_filter>
    <app_adc_conf.safe_start>1</app_adc_conf.safe_start>
    <app_adc_conf.cc_button_inverted>0</app_adc_conf.cc_button_inverted>
    <app_adc_conf.rev_button_inverted>0</app_adc_conf.rev_button_inverted>
    <app_adc_conf.voltage_inverted>0</app_adc_conf.voltage_inverted>
    <app_adc_conf.voltage2_inverted>0</app_adc_conf.voltage2_inverted>
    <app_adc_conf.throttle_exp>0</app_adc_conf.throttle_exp>
    <app_adc_conf.throttle_exp_brake>0</app_adc_conf.throttle_exp_brake>
    <app_adc_conf.throttle_exp_mode>2</app_adc_conf.throttle_exp_mode>
    <app_adc_conf.ramp_time_pos>0.3</app_adc_conf.ramp_time_pos>
    <app_adc_conf.ramp_time_neg>0.1</app_adc_conf.ramp_time_neg>
    <app_adc_conf.multi_esc>1</app_adc_conf.multi_esc>
    <app_adc_conf.tc>0</app_adc_conf.tc>
    <app_adc_conf.tc_max_diff>3000</app_adc_conf.tc_max_diff>
    <app_adc_conf.update_rate_hz>500</app_adc_conf.update_rate_hz>
    <app_uart_baudrate>115200</app_uart_baudrate>
    <app_chuk_conf.ctrl_type>1</app_chuk_conf.ctrl_type>
    <app_chuk_conf.hyst>0.15</app_chuk_conf.hyst>
    <app_chuk_conf.ramp_time_pos>0.4</app_chuk_conf.ramp_time_pos>
    <app_chuk_conf.ramp_time_neg>0.2</app_chuk_conf.ramp_time_neg>
    <app_chuk_conf.stick_erpm_per_s_in_cc>3000</app_chuk_conf.stick_erpm_per_s_in_cc>
    <app_chuk_conf.throttle_exp>0</app_chuk_conf.throttle_exp>
    <app_chuk_conf.throttle_exp_brake>0</app_chuk_conf.throttle_exp_brake>
    <app_chuk_conf.throttle_exp_mode>2</app_chuk_conf.throttle_exp_mode>
    <app_chuk_conf.multi_esc>1</app_chuk_conf.multi_esc>
    <app_chuk_conf.tc>0</app_chuk_conf.tc>
    <app_chuk_conf.tc_max_diff>3000</app_chuk_conf.tc_max_diff>
    <app_chuk_conf.use_smart_rev>1</app_chuk_conf.use_smart_rev>
    <app_chuk_conf.smart_rev_max_duty>0.07</app_chuk_conf.smart_rev_max_duty>
    <app_chuk_conf.smart_rev_ramp_time>3</app_chuk_conf.smart_rev_ramp_time>
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

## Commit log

2022-06-21 adding battery % detection
2022-06-22 workaround battery cell detection
    [receiver.ino]
2022-06-22 adding documentation
    [belt_drive_A.stl, belt_drive_B.stl, cable_guide.stl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]
2022-06-23 Update receiver.ino
    removed not wokring auto detection of vesc battery cells
    fixed dutycycle
    [receiver.ino]
2022-06-27 admin transmitter scans for existing transmitter and starts up with the same stage/pull value
2022-06-27 get into neutral winch state only with double click from brake
2022-07-08 vesc binaries and config
    [vesc_app_config.xml]
2022-07-09 pull values in kg, negative for brake
2022-07-09 absolut default pull and brake
2022-07-09 vesc app and motor config
    [vesc_app_config.xml, vesc_motor_config_12kw_260_V4.xml, vesc_motor_config_12kw_273.xml]
2022-11-09 binaries of remote controller for a LoRa32 V2.1 1.6 board
2023-10-21 Update transmitter.ino
    adding pull step down on long click on "up" button.
    since the "down/stop" button always immediately leads to default pull
